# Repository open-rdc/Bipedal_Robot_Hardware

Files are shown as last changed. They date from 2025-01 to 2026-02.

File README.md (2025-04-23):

# Bipedal_Robot_Hardware

RDC_LAB ２足歩行ロボット開発リポジトリ（ハードウェア）

## Circuit
- RDC_Bipedal_Logic
  - Logic回路基板。コンピュータや通信周り
  - Kicad Version: 7
- RDC_Bipedal_Power_Relay_Switch
  - Power回路のリレーのスイッチと、非常停止ボタンの回路
  - Kicad Version: 7
- RDC_Bipedal_Power
  - Power回路図。基板はなく回路図のみ
  - Kicad Version: 9
- RDC_CAN_Chain
  - CANのデイジーチェーン用基板
  - Kicad Version: 9

## LICECNSE

### Hardware
- designer: [Sato Tomoki](https://github.com/tomoki057)

### Circuit
- V1
  - designer: [YusukeYamasaki](https://github.com/Yusuke-Yamasaki-555)
- V2
  - RDC_Bipedal_Logic
    - designer:
      - [Yuya Mochizuki](https://github.com/Mochizuki12)
      - [YusukeYamasaki](https://github.com/Yusuke-Yamasaki-555)
  - RDC_Bipedal_Power_Relay_Switch
    - designer: [YusukeYamasaki](https://github.com/Yusuke-Yamasaki-555)
  - RDC_Bipedal_Power
    - designer: [YusukeYamasaki](https://github.com/Yusuke-Yamasaki-555)
  - RDC_CAN_Chain
    - designer: [YusukeYamasaki](https://github.com/Yusuke-Yamasaki-555)

### maintainer
- [open-rdc/Teams/Humanoid_Development_Team](https://github.com/orgs/open-rdc/teams/humanoid_development_team)

### contributor
- [open-rdc/Teams/Humanoid_Development_Team](https://github.com/orgs/open-rdc/teams/humanoid_development_team)
- [Yuya Mochizuki](https://github.com/Mochizuki12)

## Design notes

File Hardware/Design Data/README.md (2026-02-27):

# RDC-TSUKUBOの全体構成

本ロボットは、**両脚部・胴体部・外装部**の3つの要素から構成される二足歩行ロボットである。

※All Fileにロボット全体のinventorデータを保管しています。ファイルが大きかったので、3つに分けてあります。

---

# 脚部（Leg Assembly）

## ♢ HIP

- RP_Hip-Base  
- RP_Hip-Link-Right  
- RP_Hip-Link-Left  

---

## ♢ Thigh

- RP_Thigh-Base-Right  
- RP_Thigh-Base-Left  
- RP_Thigh-Link  
- RP_Thigh-Base-Cover  
- RP_Thigh-Cover  
- RP_Thigh-Cover-Connect  

---

## ♢ Calf

- RP_Calf-Link-Cover-Inside-Right  
- RP_Calf-Link-Cover-Inside-Left  
- RP_Calf-Link-Cover-Outside-Right  
- RP_Calf-Link-Cover-Outside-Left  
- RP_Calf-Link  
- RP_Calf-Foot  

---

# 胴体部（Body Assembly）

※ 今後記載予定

---

# 外装部（Exterior Assembly）

※ 今後記載予定

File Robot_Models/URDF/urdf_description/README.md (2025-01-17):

# Robot URDF

URDF kitchenを用いて生成してみる。<br>

ref:<br>
- https://qiita.com/Ninagawa123/items/c4643ca92e57c3a45efb
- https://github.com/Ninagawa123/URDF_kitchen

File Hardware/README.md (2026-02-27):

# Design Data
脚部，胴体部，外装部，全体アセンブリのCADデータを保管する

---

# 2DCAD Drawings
JLCCNC(JLCPCB)で使用した2DCAD図面を保管する

---

# stp files
3Dプリンタや、JLCCNC(JLCPCB)で使用したstpファイルを保管する

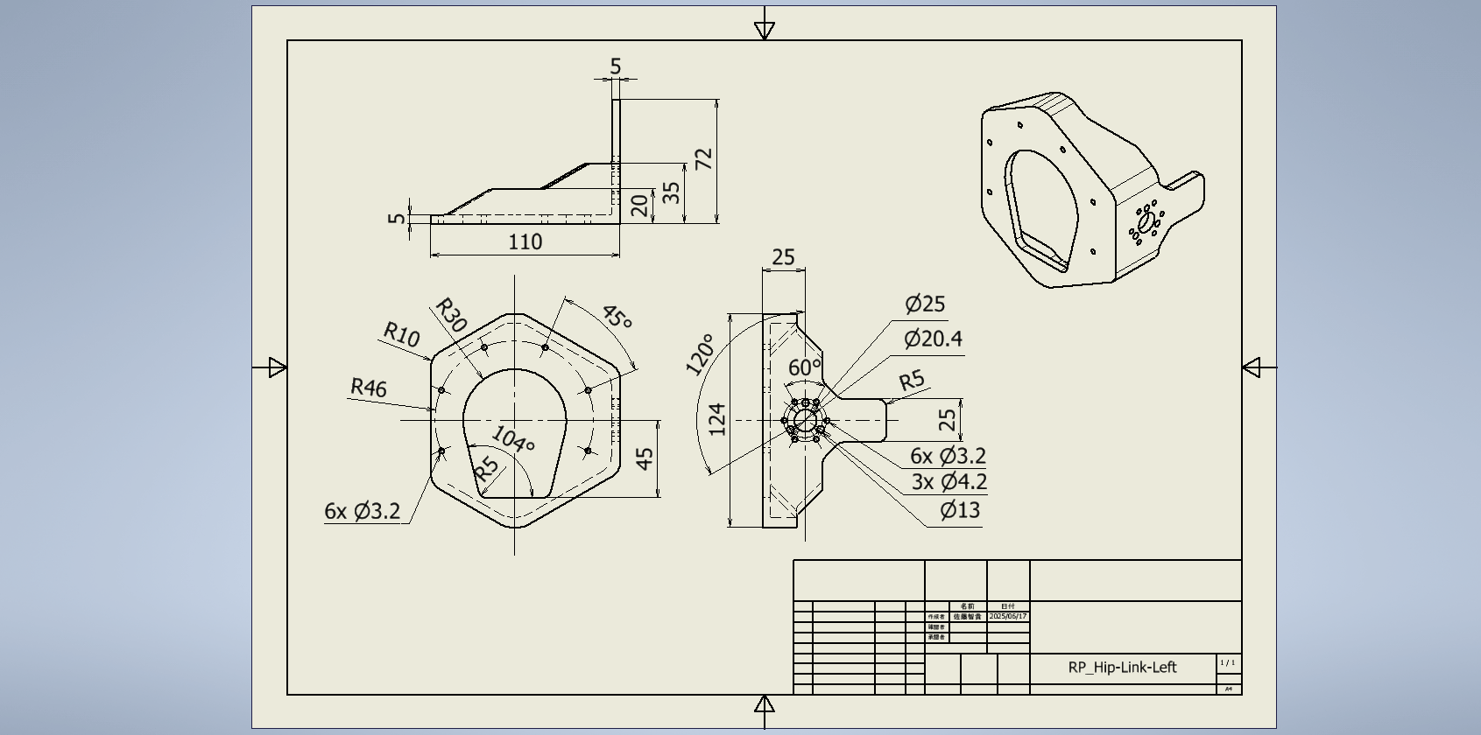
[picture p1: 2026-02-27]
Hardware/2D CAD Drawing/RP_Hip-Link-Left.png

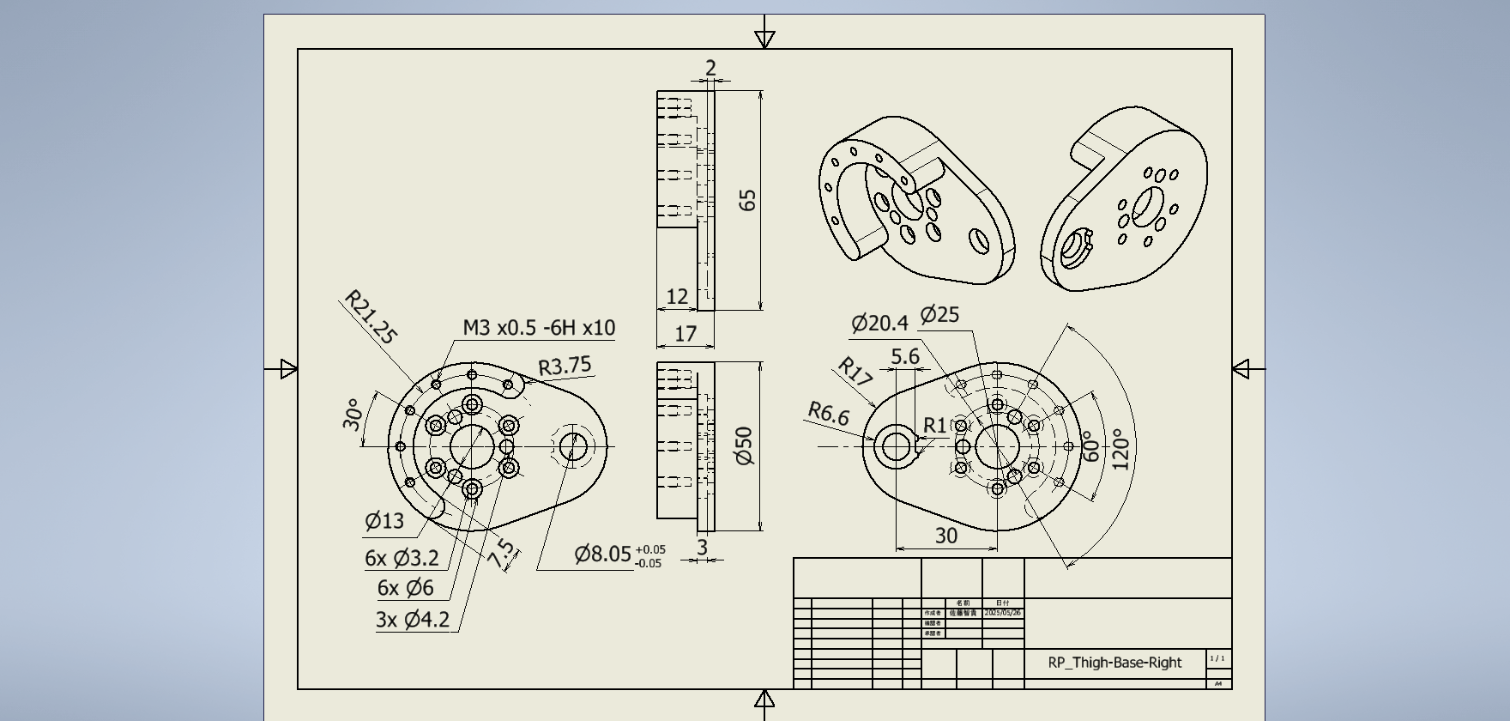
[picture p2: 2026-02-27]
Hardware/2D CAD Drawing/RP_Thigh-Base-Right.png

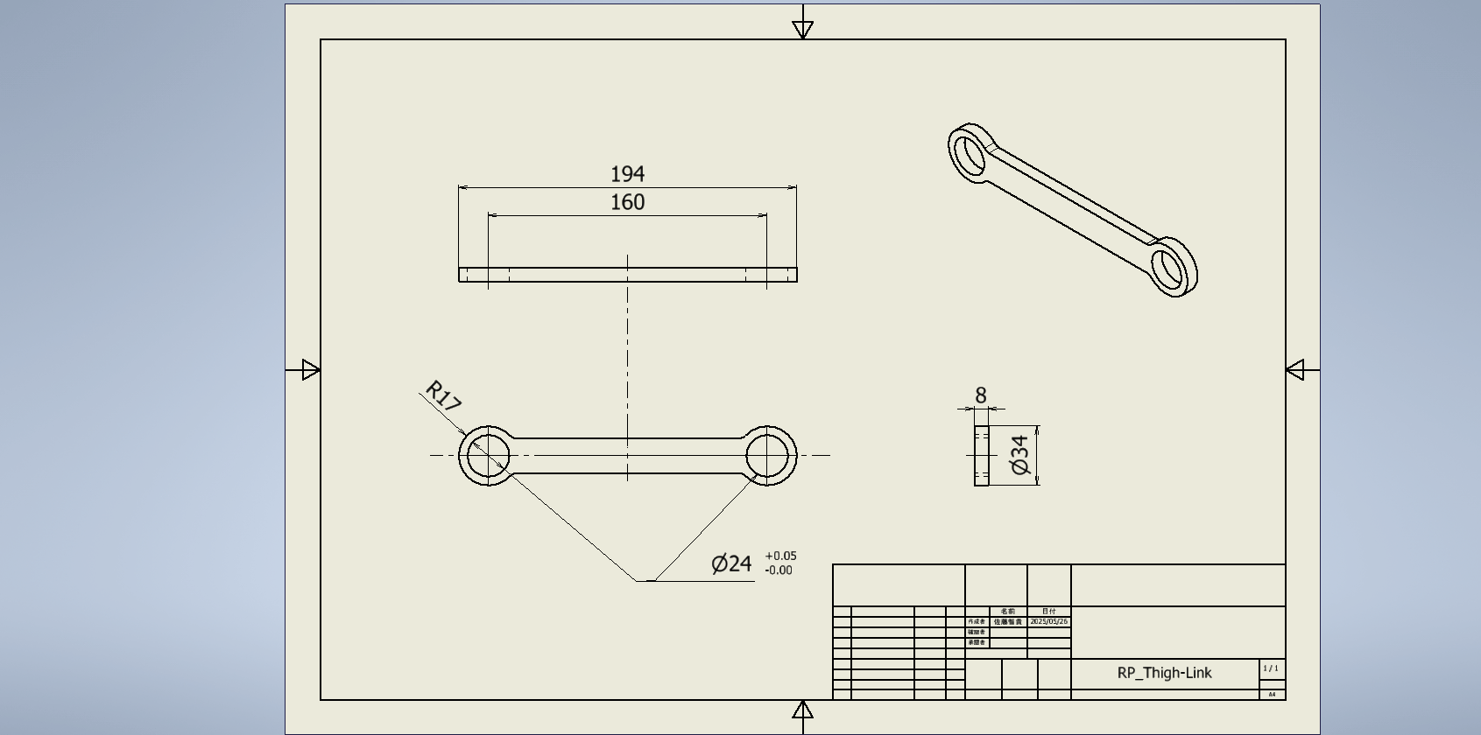
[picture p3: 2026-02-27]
Hardware/2D CAD Drawing/RP_Thigh-Link.png

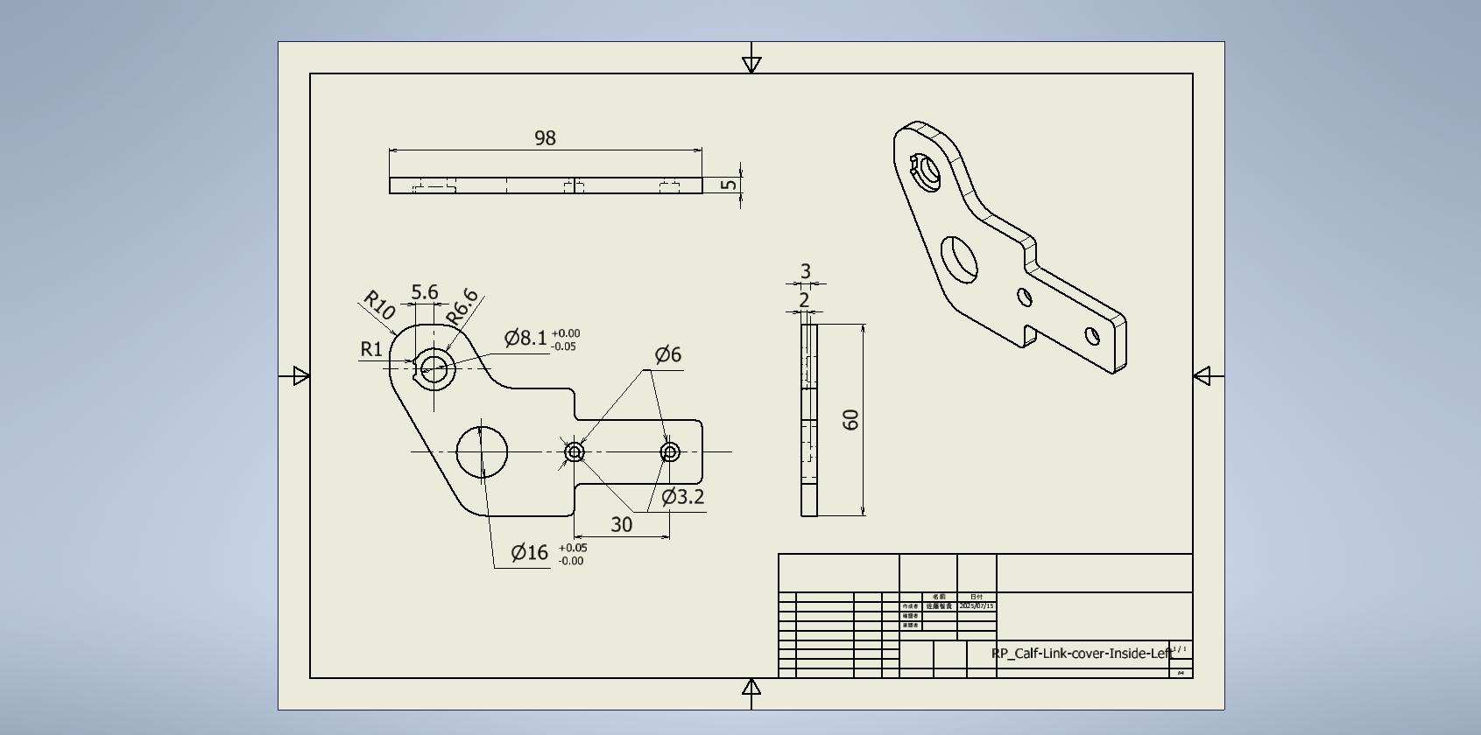
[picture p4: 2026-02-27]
Hardware/2D CAD Drawing/RP_Calf-Link-cover-Inside-Left.png

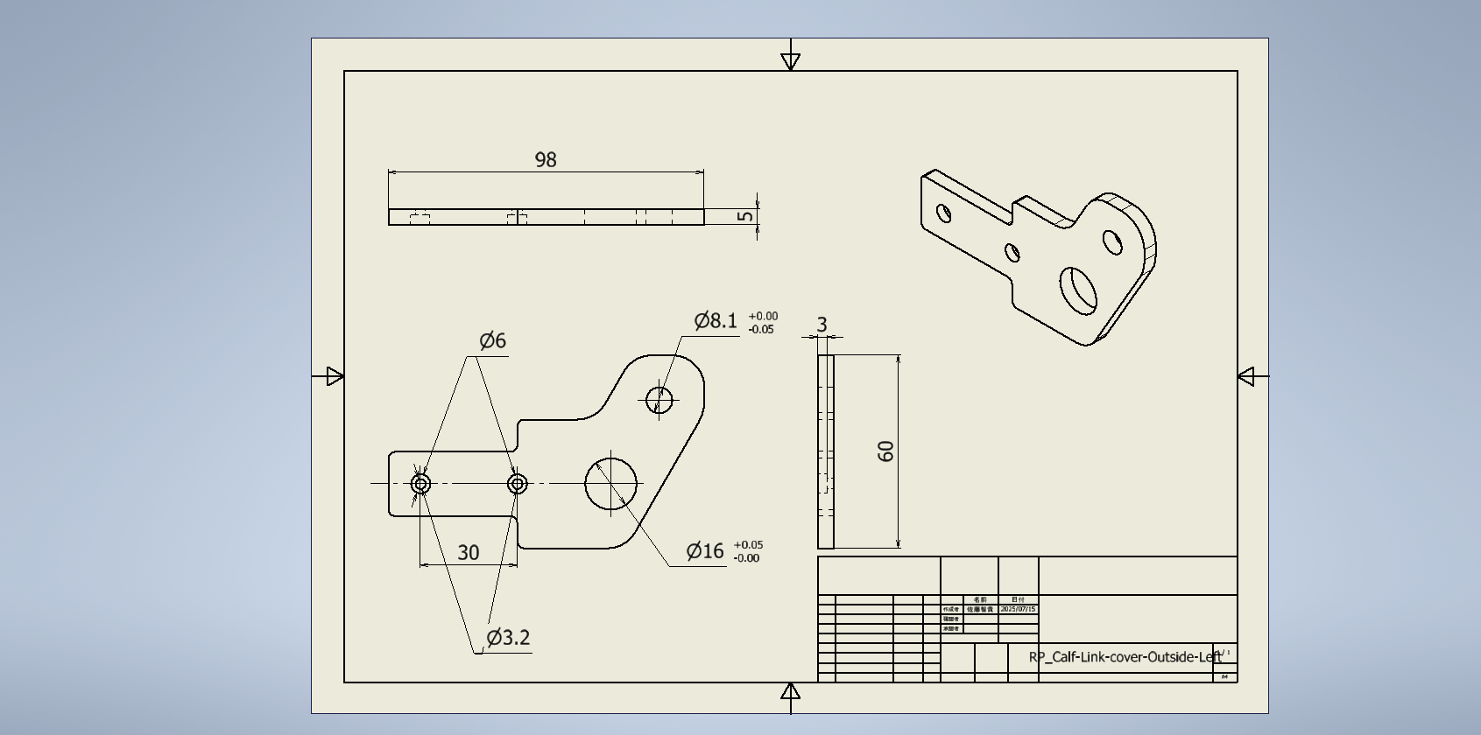
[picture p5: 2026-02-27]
Hardware/2D CAD Drawing/RP_Calf-Link-cover-Outside-Left.png

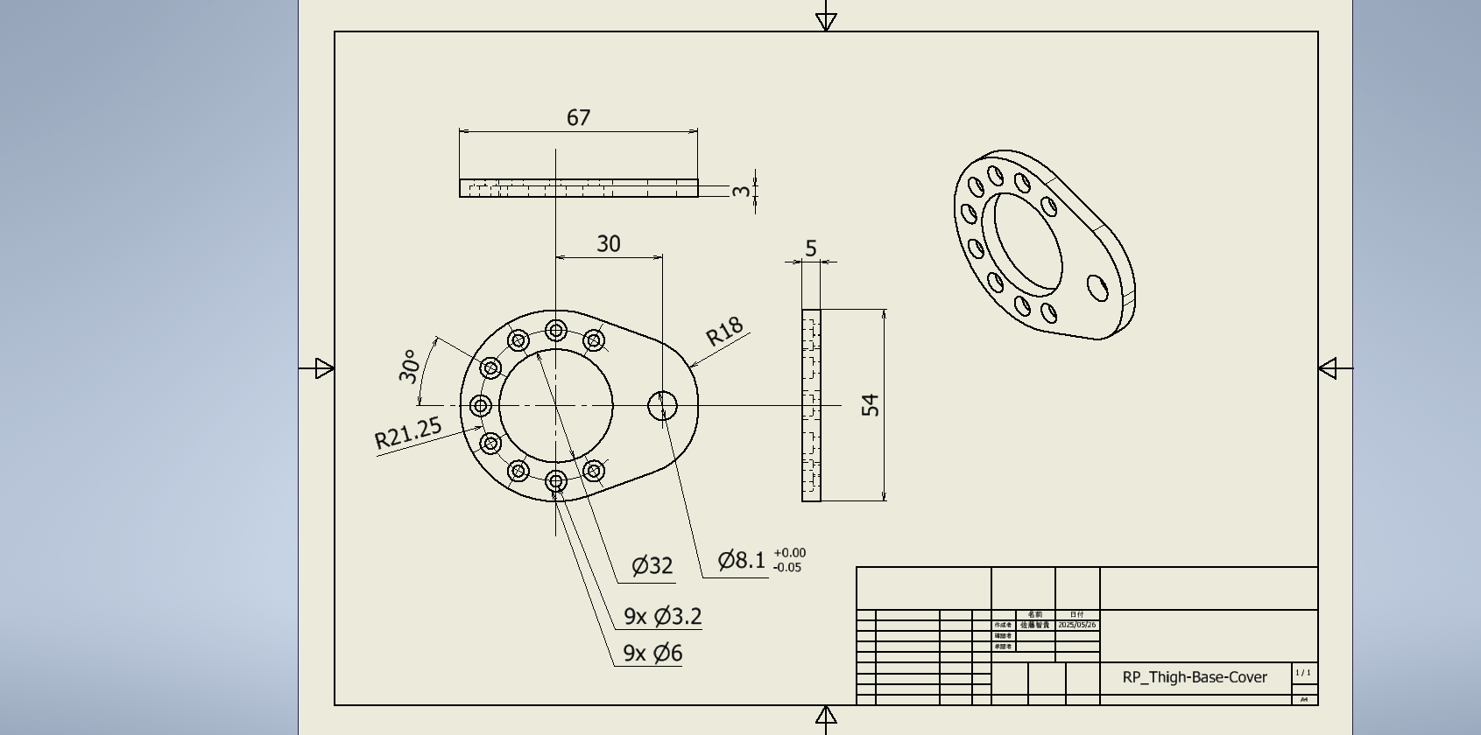
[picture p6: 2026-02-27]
Hardware/2D CAD Drawing/RP_Thigh-Base-Cover.png

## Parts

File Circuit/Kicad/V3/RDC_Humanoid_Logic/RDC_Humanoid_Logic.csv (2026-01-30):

Reference | Qty | Value | DNP | Exclude from BOM | Exclude from Board | Footprint | Datasheet
C1 | 1 | 100uF |  |  |  | Capacitor_THT:CP_Radial_D6.3mm_P2.50mm | https://akizukidenshi.com/catalog/g/g102724/
C2,C6,C7,C15,C16 | 5 | 0.1uF |  |  |  | Capacitor_SMD:C_0603_1608Metric | ~
C3,C9,C11,C12,C18,C20 | 6 | 10uF |  |  |  | Capacitor_SMD:C_0603_1608Metric | ~
C4,C10,C13,C19 | 4 | 1uF |  |  |  | Capacitor_SMD:C_0603_1608Metric | ~
C5,C8,C14,C17 | 4 | 10nF |  |  |  | Capacitor_SMD:C_0603_1608Metric | ~
D1 | 1 | D_Schottky |  |  |  | Diode_SMD:D_SOD-123 | ~
D2,D3,D4 | 3 | LED |  |  |  | LED_SMD:LED_0603_1608Metric | ~
FB1,FB2,FB3,FB4,FB5,FB6,FB7,FB8,FB9,FB10 | 10 | FerriteBead |  |  |  | Inductor_SMD:L_0805_2012Metric | ~
for_PG1 | 1 | M78AR05-0.5 |  |  |  | RDC_humanoid_project:M78A
H1,H2,H3,H4 | 4 | MountingHole |  |  |  | MountingHole:MountingHole_3.2mm_M3 | ~
J1 | 1 | XT60 |  |  |  | Connector_AMASS:AMASS_XT60PW-M_1x02_P7.20mm_Horizontal | ~
J2,J3 | 2 | Conn_01x03 |  |  |  | Connector_JST:JST_XA_S03B-XASK-1_1x03_P2.50mm_Horizontal | https://www.jst-mfg.com/product/pdf/eng/eXA-WB.pdf?67d6871ee54a2
J4 | 1 | Raspi_connect |  |  |  | Connector_PinHeader_2.54mm:PinHeader_2x20_P2.54mm_Vertical | ~
J5 | 1 | 74AHC1G04W5 |  |  |  | Package_TO_SOT_SMD:SOT-23-5 | https://akizukidenshi.com/goodsaffix/74ahc1g04.pdf
J6,J7 | 2 | CH213K |  |  |  | Package_TO_SOT_SMD:SOT-23-3 | https://akizukidenshi.com/goodsaffix/CH213.pdf
Q1,Q2 | 2 | Q_PMOS_GDS |  |  |  | Package_TO_SOT_SMD:TO-252-2 | https://akizukidenshi.com/goodsaffix/TJ60S04M3L_datasheet_ja_20200624.pdf
R1,R2,R7,R8,R12,R13,R14,R15 | 8 | 10k |  |  |  | Resistor_SMD:R_0603_1608Metric | ~
R3,R5,R9 | 3 | 4.7k |  |  |  | Resistor_SMD:R_0603_1608Metric | ~
R4,R6 | 2 | 120 |  |  |  | Resistor_SMD:R_0603_1608Metric | ~
R10,R11 | 2 | 1k |  |  |  | Resistor_SMD:R_0603_1608Metric | ~
SW1,SW2,SW3 | 3 | SW_SPDT |  |  |  | RDC_humanoid_project:Toggle_switch | https://akizukidenshi.com/goodsaffix/2MS1-T1-B4-VS2-Q-E-S.pdf
to_RPI1,to_STM1 | 2 | AE-MYMGK00506ERSR-5V0 |  |  |  | RDC_humanoid_project:AE-MYMGK00506ERSR-5V0
U1,U2 | 2 | ISOW1044 |  |  |  | Package_SO:SOIC-20W_7.5x12.8mm_P1.27mm | https://www.ti.com/lit/ds/symlink/isow1044.pdf?ts=1742141302334
U3 | 1 | NUCLEO-H755ZI-Q_Zio |  |  |  | RDC_humanoid_project:NUCLEO-STM32H755ZI-Q
U4 | 1 | TBD62083AFG |  |  |  | Package_SO:SOP-18_7.495x11.515mm_P1.27mm | https://toshiba.semicon-storage.com/info/datasheet_ja_20160511.pdf?did=29808

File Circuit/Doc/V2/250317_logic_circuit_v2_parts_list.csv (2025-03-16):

 | 私費購入予定 |  |  | 合計金額
↓：要変更 |  |  |  | ¥ 11,558.50 |  |  |  |  | ←：セット商品
 | 購入済み | 系統 | 部品名・部品用途 | 商品名 | 発注会社 | 購入リンク(URL) | 価格(税込み) | 必要数量（最低） | 購入数量 | 購入金額 | 単体重量 [kg] | 総重量 [kg] | 重量（＆関するコメント） | コメント
 | FALSE | コネクタ | 電源用。XT60PW-M | XT60コネクター オス 基板取付用 XT60PW-M | 秋月電子 | https://akizukidenshi.com/catalog/g/g118156/ | ¥ 100.00 | 1 | 1 | ¥ 100.00 |  | 0
 | FALSE | コネクタ | CAN通信用XAヘッダ。S03B-XASK-1 | S03B-XASK-1 | marutsu | https://www.marutsu.co.jp/pc/i/2231712/ | ¥ 67.00 | 2 | 2 | ¥ 134.00 |  | 0 |  | XAコネクタの仕様書：JSTリンク
 | FALSE | コネクタ | CAN通信用XAハウジング。XAP-03V-1 | XAP-03V-1 | marutsu | https://www.marutsu.co.jp/pc/i/953235/ | ¥ 40.00 | 2 | 2 | ¥ 80.00 |  | 0
 | FALSE | コネクタ | CAN通信用XAコンタクト。SXA-001T-P0.6 | SXA-001T-P0.6 | marutsu | https://www.marutsu.co.jp/pc/i/574398/ | ¥ 24.00 | 6 | 6 | ¥ 144.00 |  | 0 |  | コンタクトはまとめ買いのほうがお得なので、それに変えたほうが良い。
 | FALSE | ピンヘッダ | PinHeader_2x20_P2.54mm | ピンヘッダー2x20 (40P) | 秋月電子 | https://akizukidenshi.com/catalog/g/g100080/ | ¥ 50.00 | 1 | 1 | ¥ 50.00 |  | 0
 | TRUE | DCDCコンバータ | 12Vto5V大電流対応降圧モジュール | MYMGK00506ERSR使用 5V出力 最大6A 大電流DCDCコンバーターモジュールキット | 秋月電子 | https://akizukidenshi.com/catalog/g/g115108/ | ¥ 1,320.00 | 2 | 0 | ¥ - |  | 0
 | FALSE | DCDCコンバータ | 12Vto5V PG用DCDCパッケージ | 超高効率DCDCコンバーター(5V0.5A) M78AR05-0.5 | 秋月電子 | https://akizukidenshi.com/catalog/g/g107179/ | ¥ 580.00 | 1 | 1 | ¥ 580.00 | 0.00195 | 0.00195
 | FALSE | スイッチ | 1回路２接点コンピュータ電源用スイッチ | 基板用小型3Pトグルスイッチ 1回路2接点 | 秋月電子 | https://akizukidenshi.com/catalog/g/g100300/ | ¥ 140.00 | 3 | 3 | ¥ 420.00 |  | 0
 | FALSE | コンデンサ | 電源ノイズ対策用コンデンサ | 電源用電解コンデンサー100μF35V105℃ ルビコンZLH | 秋月電子 | https://akizukidenshi.com/catalog/g/g102724/ | ¥ 15.00 | 1 | 1 | ¥ 15.00 |  | 0
 | FALSE | トランジスタ | トランジスタアレイ | 8chソースタイプDMOSトランジスターアレイ TBD62783AFG | 秋月電子 | https://akizukidenshi.com/catalog/g/g111082 | ¥ 70.00 | 1 | 1 | ¥ 70.00 |  | 0
 | FALSE | FET | Back2Backスイッチング用PMOS | PchパワーMOSFET 40V60A TJ60S04M3L | 秋月電子 | https://akizukidenshi.com/catalog/g/g116297/ | ¥ 100.00 | 2 | 2 | ¥ 200.00 |  | 0 |  | 秋月電子で買うから、今のコレ。ゲート・ソース間電圧の定格に近づくほどドレイン・ソース間電圧（＝ロス）が減る。まあ、コレでもほとんど変わらんぐらいなので、良いんでない？
 | FALSE | 抵抗 | チップ抵抗10kΩ（主にPull Up/Down） | RMCF0603FT10K0 | Mouser | https://www.mouser.jp/ProductDetail/SEI-Stackpole/RMCF0603FT10K0 | ¥ 18.70 | 8 | 8 | ¥ 149.60 |  | 0 |  | 複数個買った方がめっちゃ割安。リール（5000個）で買うならコッチ（秋月。仕様が少し違うが問題ない。以下同様）：チップ抵抗 1/10W 10kΩ ￥980
 | FALSE | 抵抗 | チップ抵抗1kΩ（LED） | RMCF0603FT1K00 | Mouser | https://www.mouser.jp/ProductDetail/SEI-Stackpole/RMCF0603FT1K00 | ¥ 18.70 | 2 | 2 | ¥ 37.40 |  | 0 |  | 複数個買った方がめっちゃ割安。リールならコッチ：チップ抵抗 1/10W 1kΩ ￥980
 | FALSE | 抵抗 | チップ抵抗4.7kΩ（LED、Pull Up） | RMCF0603FT4K70 | Mouser | https://www.mouser.jp/ProductDetail/SEI-Stackpole/RMCF0603FT4K70 | ¥ 18.70 | 3 | 3 | ¥ 56.10 |  | 0 |  | 複数個買った方がめっちゃ割安。リールならコッチ：チップ抵抗 1/10W 4.7kΩ ￥980
 | FALSE | 抵抗 | チップ抵抗120Ω（CANの終端抵抗） | RMCF0603FT120R | Mouser | https://www.mouser.jp/ProductDetail/SEI-Stackpole/RMCF0603FT120R?qs=FESYatJ8odLT3vCYyOeKQw%3D%3D | ¥ 18.70 | 2 | 2 | ¥ 37.40 |  | 0 |  | 複数個買った方がめっちゃ割安。
 | FALSE | LED | チップLED（赤＝電源用） | 赤色チップLED [1608] 625nm 120度 OSHR1608（１パック２０個入り） | 秋月電子 | https://akizukidenshi.com/catalog/g/g103978/ | ¥ 200.00 | 1 | 1 | ¥ 200.00 |  | 0 |  | １パック２０個入りの内、実装には３個必要。
 | FALSE | ダイオード | 逆接防止用ショットキーバリアダイオード | チップダイオード 1000V1A GS1010FL（１パック１０個入り） | 秋月電子 | https://akizukidenshi.com/catalog/g/g106014/ | ¥ 100.00 | 1 | 1 | ¥ 100.00 |  | 0 |  | 逆接時に破損してほしいので、安めのやつを選定。１パック１０個の内、実装では１つ使用。
 | FALSE | ダイオード | 逆流防止用ショットキーバリアダイオード | SBRダイオード SBR2U30P1（１パック４個入り） | 秋月電子 | https://akizukidenshi.com/catalog/g/g117096/ | ¥ 100.00 | 1 | 1 | ¥ 100.00 |  | 0 |  | できる限り電圧降下を抑えたいので、順方向電圧が低い良いものを選定。１パック４個の内、使うのは１つ。
 | FALSE | コンデンサ | CAN_Trans用ノイズ対策（高周波） | チップ積層セラミックコンデンサー 0.01μF50V B 1608（１パック５０個入り） | 秋月電子 | https://akizukidenshi.com/catalog/g/g113387/ | ¥ 100.00 | 1 | 1 | ¥ 100.00 |  | 0 |  | １パックの内、実装するのは４個。
 | FALSE | コンデンサ | CAN_Trans用ノイズ対策（高～中周波）、RC回路を形成し電源投入時の電流の立ち上がりを鈍化（突入電流の抑制） | チップ積層セラミックコンデンサー 0.1μF100V X7R 1608（１パック２０個入り） | 秋月電子 | https://akizukidenshi.com/catalog/g/g114559/ | ¥ 150.00 | 1 | 1 | ¥ 150.00 |  | 0 |  | １パックの内、実装するのは５個。
 | FALSE | コンデンサ | CAN_Trans用ノイズ対策（中周波） | チップ積層セラミックコンデンサー 1μF25V X6S 1608（１パック４０個入り） | 秋月電子 | https://akizukidenshi.com/catalog/g/g116993/ | ¥ 120.00 | 1 | 1 | ¥ 120.00 |  | 0 |  | １パックの内、実装するのは４個。
 | FALSE | コンデンサ | CAN_Trans用ノイズ対策（低周波） | チップ積層セラミックコンデンサー 10μF35V X5R 1608（１パック１０個入り） | 秋月電子 | https://akizukidenshi.com/catalog/g/g113161/ | ¥ 150.00 | 1 | 1 | ¥ 150.00 |  | 0 |  | １パックの内、実装するのは６個。
 | FALSE | フェライトビーズ | CAN_Trans用ノイズ対策 | チップインダクター(フェライトビーズ) 330Ω[2012] ムラタBLM21P（１パック２５個入り） | 秋月電子 | https://akizukidenshi.com/catalog/g/g104053/ | ¥ 100.00 | 1 | 1 | ¥ 100.00 |  | 0 |  | １パックの内、実装するのは１０個。
 | TRUE | コンピュータ | 高レベル処理 | Raspberry Pi 5 (8GB) | - | - | ¥ - | 1 | 0 | ¥ - |  | 0
 | FALSE | コンピュータ | 低レベル処理 | NUCLEO-H755ZI-Q | Mouser | https://www.mouser.jp/ProductDetail/STMicroelectronics/NUCLEO-H755ZI-Q?qs=%252B6g0mu59x7KOiBeEHDTYVQ%3D%3D | ¥ 5,264.00 | 1 | 1 | ¥ 5,264.00 |  | 0
 | FALSE | その他 | 基板固定用M3スペーサ | （アキバで調達） |  |  |  |  |  | ¥ - |  | 0
 | FALSE | その他 | 基板固定用M3ナット | （アキバで調達） |  |  |  |  |  | ¥ - |  | 0
 | FALSE | その他 | 基板固定用M3ねじ | （アキバで調達） |  |  |  |  |  | ¥ - |  | 0
 | FALSE | その他 | NUCLEO用ヒートシンク | （アキバで調達） |  |  |  |  |  | ¥ - |  | 0
 | FALSE | IC | 絶縁DCDCコンバータ付き絶縁CANトランシーバ | ISOW1044BDFMR | Mouser | https://www.mouser.jp/ProductDetail/Texas-Instruments/ISOW1044BDFMR?qs=Li%252BoUPsLEnsRP1xV2fQwnw%3D%3D | ¥ 1,600.50 | 2 | 2 | ¥ 3,201.00 |  | 0
 | FALSE |  |  |  |  |  |  |  |  | ¥ - |  | 0
 | FALSE |  |  |  |  |  |  |  |  | ¥ - |  | 0
 | FALSE |  |  |  |  |  |  |  |  | ¥ - |  | 0
 | FALSE |  |  |  |  |  |  |  |  | ¥ - |  | 0
 | FALSE |  |  |  |  |  |  |  |  | ¥ - |  | 0
 | FALSE |  |  |  |  |  |  |  |  | ¥ - |  | 0
 | FALSE |  |  |  |  |  |  |  |  | ¥ - |  | 0
 | FALSE |  |  |  |  |  |  |  |  | ¥ - |  | 0
 | FALSE |  |  |  |  |  |  |  |  | ¥ - |  | 0
 | FALSE |  |  |  |  |  |  |  |  | ¥ - |  | 0
 | FALSE |  |  |  |  |  |  |  |  | ¥ - |  | 0
 |  |  |  |  |  |  |  |  | 最低合計金額： | ¥11,558.50
 |  |  |  |  |  |  |  | 購入先別金額 | 秋月電子： | ¥ 2,455.00 |  | 送料リスト： | Mouser： | ¥2,000.00
 |  |  |  |  |  |  |  |  | Mouser： | ¥ 8,745.50 |  | （税込み） | 秋月電子： | 500 or 600 x 個口数
 |  |  |  |  |  |  |  |  | marutsu： | ¥ 358.00 |  |  | marutsu： | 550 (宅急便) or 385 (ネコポス)
 |  |  |  |  |  |  |  |  |  |  |  | 送料無料ライン： | Mouser： | ¥6,600.00
 |  |  |  |  |  |  |  |  | SUM | ¥ 11,558.50 |  | （税込み） | 秋月電子： | ¥11,000.00
 |  |  |  |  |  |  |  |  |  |  |  |  | marutsu： | ¥3,300.00

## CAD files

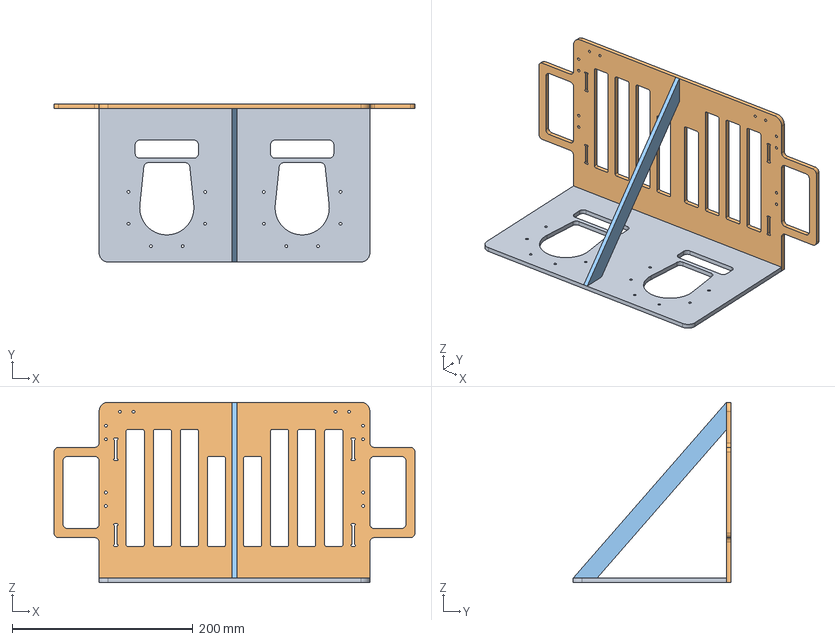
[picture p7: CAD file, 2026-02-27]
Hardware/stp files/Assembly_Waist.stp
400.0 x 175.0 x 200.0 mm
RP_Waist-Under
RP_Waist-Avobe
RP_Waist-Diagonal-material

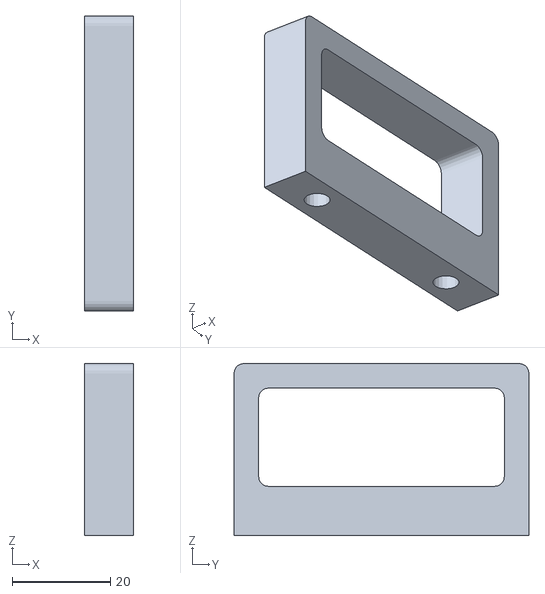
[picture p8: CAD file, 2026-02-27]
Hardware/Design Data/Body Assembly/BP_BOX-handle.stl
10.0 x 60.0 x 35.0

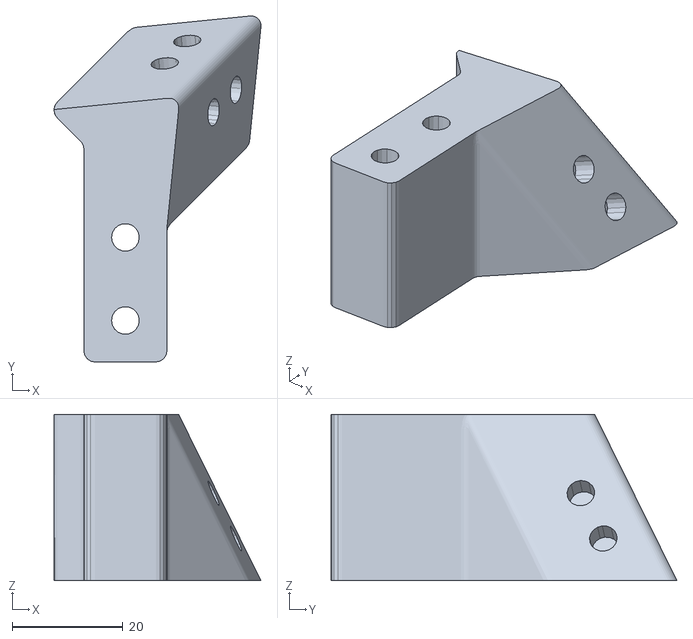
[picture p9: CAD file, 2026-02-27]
Hardware/Design Data/Exterior Assembly/EX-L-Connect-Back-Right.stl
37.4 x 62.5 x 30.0

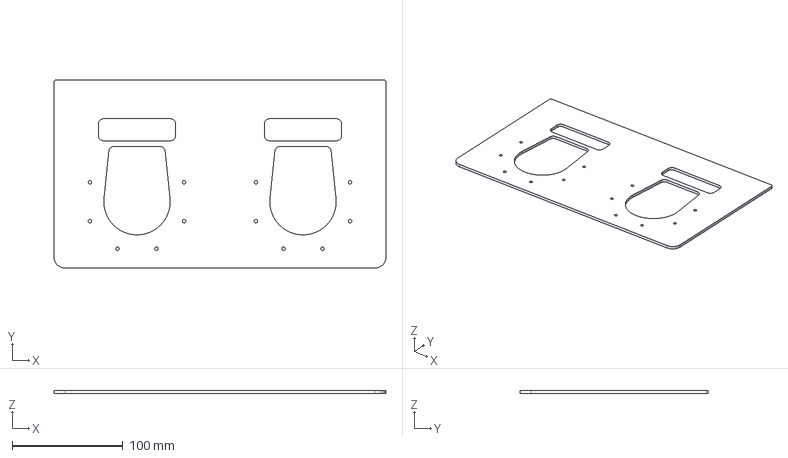
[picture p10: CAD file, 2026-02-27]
Hardware/Design Data/Leg Assembly/RP_Waist-Under-ver2.stp
300.0 x 170.0 x 3.00 mm

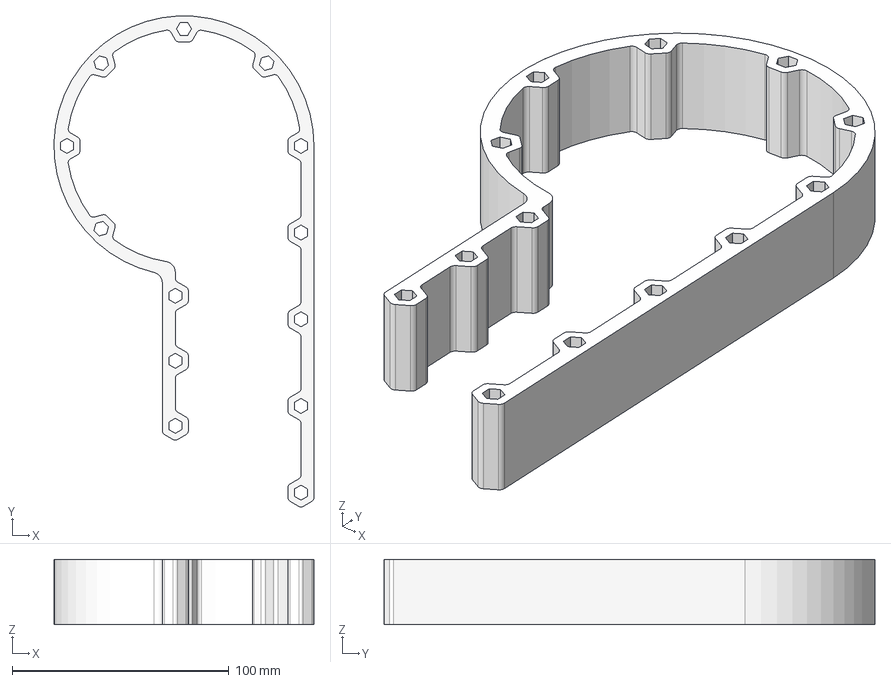
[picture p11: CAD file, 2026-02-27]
Hardware/stp files/RP_Thigh-cover-connect.stp
120.0 x 226.5 x 30.0 mm

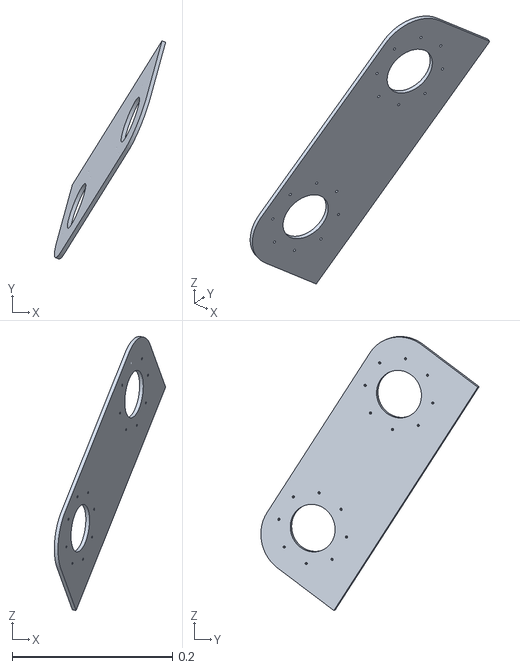
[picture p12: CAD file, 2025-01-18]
Robot_Models/URDF/urdf_description/meshes/body/b_right-wr2left-wr__legparts_09(six).stl
0.139 x 0.273 x 0.342

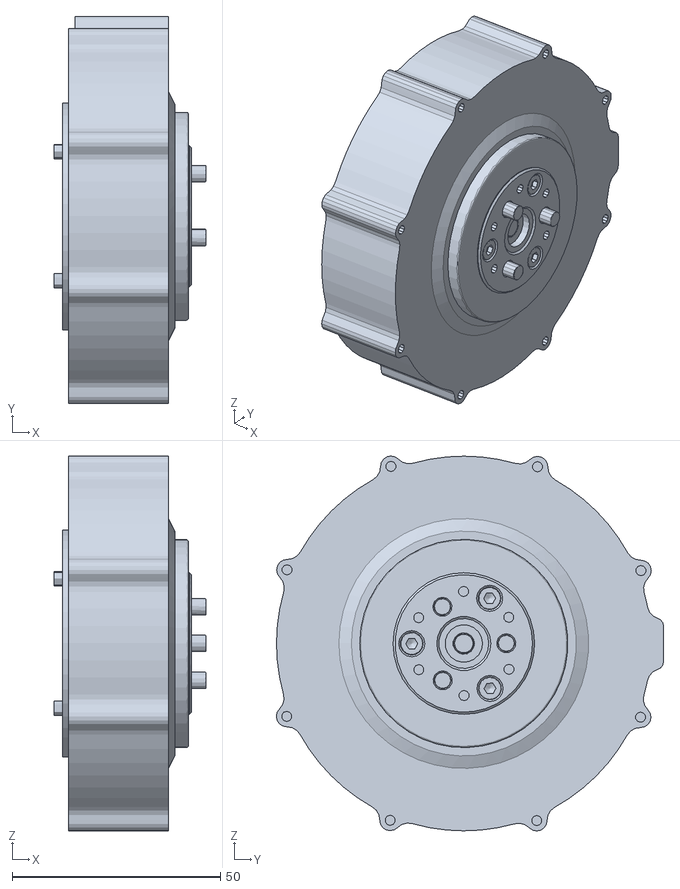
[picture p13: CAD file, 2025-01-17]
Robot_Models/URDF/urdf_description/meshes/r-leg/mm/mr_j_wr__8108-8.stl
36.5 x 93.0 x 90.1

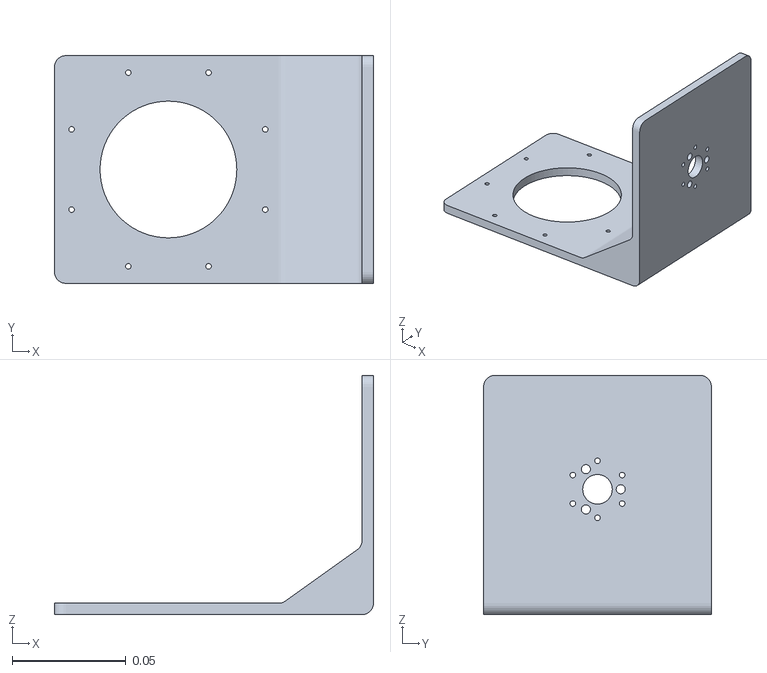
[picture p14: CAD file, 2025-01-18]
Robot_Models/URDF/urdf_description/meshes/r-leg/r_l_wp2wr__legparts_07(four).stl
0.14 x 0.1 x 0.105

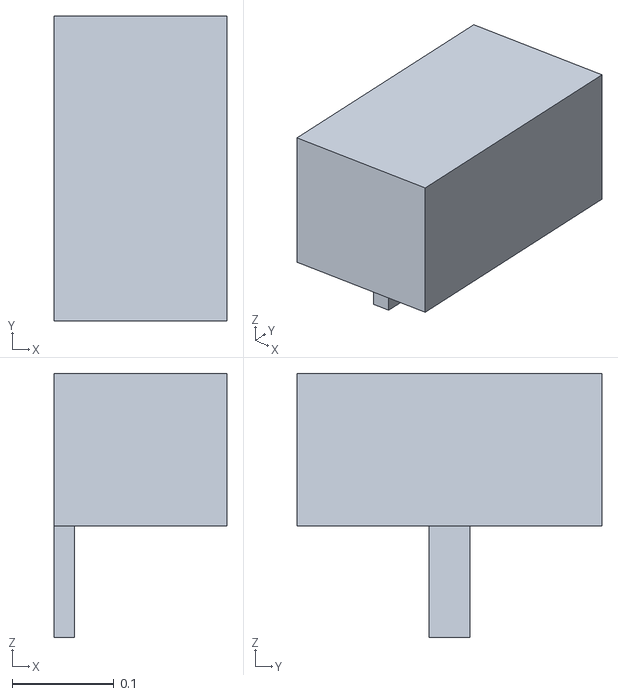
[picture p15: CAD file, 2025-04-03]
Robot_Models/URDF/urdf_simple-model/meshes/stl/body_luggage.stl
0.17 x 0.3 x 0.26

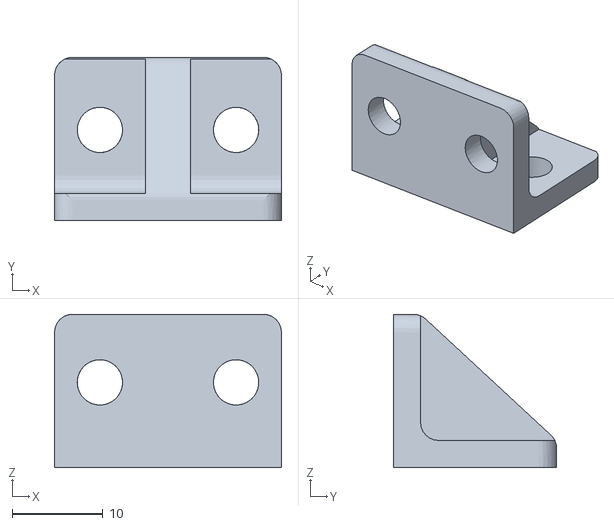
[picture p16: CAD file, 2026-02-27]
Hardware/Design Data/Body Assembly/BP_L.stl
25.0 x 18.0 x 16.9

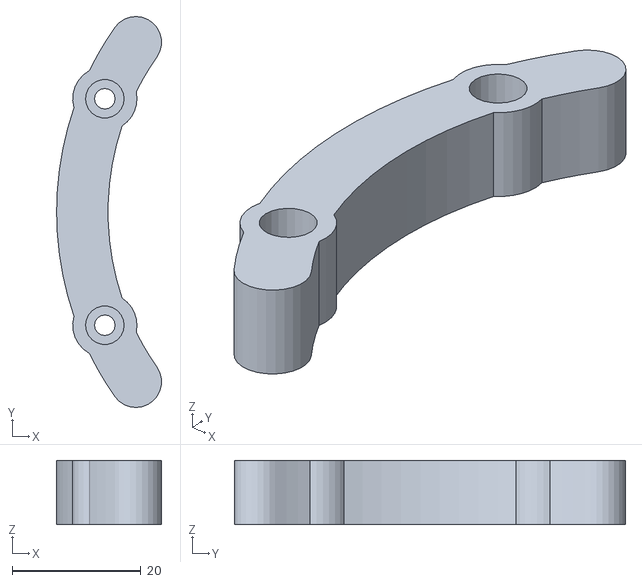
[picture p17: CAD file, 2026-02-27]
Hardware/Design Data/Leg Assembly/RP_Hip-Link-Limit-short.stl
16.3 x 60.8 x 10.0

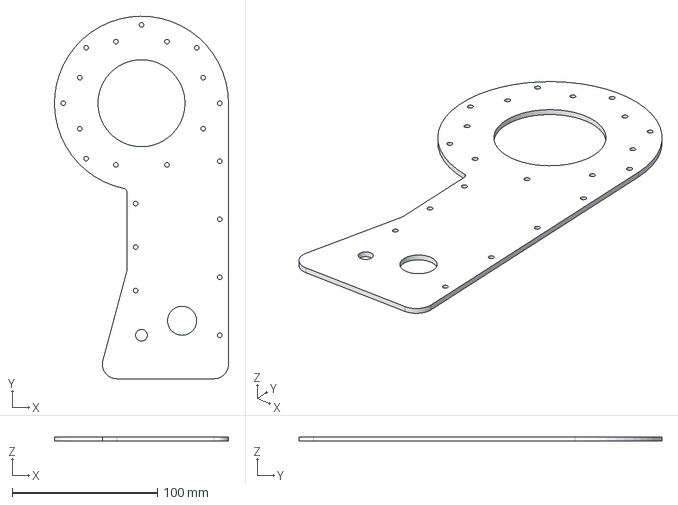
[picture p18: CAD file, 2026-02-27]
Hardware/stp files/RP_Thigh-cover.stp
120.0 x 250.0 x 3.00 mm

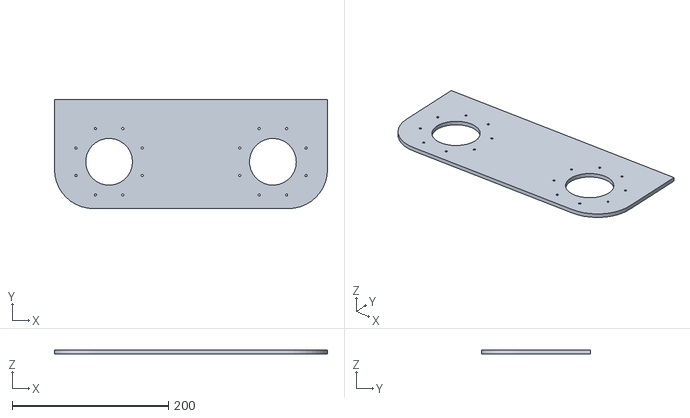
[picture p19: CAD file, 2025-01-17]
Robot_Models/URDF/urdf_description/meshes/body/mb_right-wr2left-wr__legparts_09(six).stl
350.0 x 140.0 x 5.00

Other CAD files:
Hardware/2D CAD Drawing/Assembly_All.dwg
Hardware/2D CAD Drawing/Assembly_Leg-Right.dwg
Hardware/2D CAD Drawing/RP_Hip-Link-Left.dwg
Hardware/2D CAD Drawing/RP_Hip-Base.dwg
Hardware/Design Data/Exterior Assembly/EX-L-Connect-Back-Left.stl
Hardware/2D CAD Drawing/AA30306.dwg
Hardware/2D CAD Drawing/RP_Calf-Link-cover-Inside-Left.dwg
Hardware/2D CAD Drawing/RP_Calf-Link-cover-Inside-Right.dwg
Hardware/2D CAD Drawing/RP_Calf-Link-cover-Outside-Left.dwg
Hardware/2D CAD Drawing/RP_Calf-Link-cover-Outside-Right.dwg
Hardware/2D CAD Drawing/RP_Hip-Link-Right.dwg
Hardware/2D CAD Drawing/RP_Thigh-Base-Cover.dwg
Hardware/2D CAD Drawing/RP_Thigh-Base-Right.dwg
Hardware/2D CAD Drawing/RP_Thigh-Base_Left.dwg
Hardware/2D CAD Drawing/RP_Thigh-Link.dwg
Hardware/2D CAD Drawing/RP_Thigh-cover.dwg
Hardware/2D CAD Drawing/RP_Waist-Avobe-ver2-1.dwg
Hardware/2D CAD Drawing/RP_Waist-Under-ver2.dwg
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

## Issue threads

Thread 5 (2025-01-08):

SteadyWin GIM8108-8を動かしてみる

HarukiOgawa1, 2025-01-08:
## 動作環境
Steadywin-GIM8108-8
安定化電源 (SPS-3010 0-30V 0-10A)
USBケーブル (type A to C)
XT30PB(2+2)-M

## やること

- [x] とりあえず、電源とUSB通信して動かす

- [x] そのあと、CAN通信で動かす

- [x] 動作環境を整える

　安定化電源　（KX-100L）
　USBケーブル
　電源ケーブル　https://www.amazon.co.jp/dp/B08FSYZBTD?ref=ppx_yo2ov_dt_b_fed_asin_title
　XT30PB(2+2)-M　受けに合うように
　XT30(2+2)-F メス
　CANケーブル　https://www.amazon.co.jp/dp/B0BQ5G3KLR?ref=ppx_yo2ov_dt_b_fed_asin_title

## 参考
[Steadywin-GIM8108-8を回す odrivetool編](https://zenn.dev/robohase01/articles/6eae2db2af93d8)
[Steadywin-GIM8108-8を回す ROS 2編](https://zenn.dev/robohase01/articles/4697e25ca87c76)

HarukiOgawa1, 2025-01-08:
wslの場合
- wslで行う場合
https://learn.microsoft.com/ja-jp/windows/wsl/connect-usb
USBに接続して許可する　Sharedはまだ使えない状態
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

```
PS C:\Users\azara> usbipd list
Connected:
BUSID  VID:PID    DEVICE                                                        STATE
1-2    1209:0d32  USB シリアル デバイス (COM4), CyberBeast Motor Driver Device          Shared
1-3    04f2:b725  Integrated Camera, Camera DFU Device                          Not shared
2-1    0000:3825  USB 入力デバイス                                                    Not shared
2-3    27c6:550a  Goodix fingerprint                                            Not shared
2-4    0bda:4853  Realtek Bluetooth Adapter                                     Shared

Persisted:
GUID                                  DEVICE
6e8e7fe5-4833-43df-853f-f201de69bc54  USB Serial Converter A, USB Serial Converter B, USB Seria...

PS C:\Users\azara> usbipd attach --wsl --busid 1-2
usbipd: info: Using WSL distribution 'Ubuntu-22.04' to attach; the device will be available in all WSL 2 distributions.
usbipd: info: Using IP address 172.26.64.1 to reach the host.
PS C:\Users\azara> usbipd list
Connected:
BUSID  VID:PID    DEVICE                                                        STATE
1-2    1209:0d32  USB シリアル デバイス (COM4), CyberBeast Motor Driver Device          Attached
1-3    04f2:b725  Integrated Camera, Camera DFU Device                          Not shared
2-1    0000:3825  USB 入力デバイス                                                    Not shared
2-3    27c6:550a  Goodix fingerprint
    Not shared
2-4    0bda:4853  Realtek Bluetooth Adapter
    Shared

Persisted:
GUID                                  DEVICE
6e8e7fe5-4833-43df-853f-f201de69bc54  USB Serial Converter A, USB Serial Converter B, USB Seria...

```

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

Yusuke-Yamasaki-555, 2025-01-26:
メモ:
odrive can bus guide: https://docs.odriverobotics.com/v/latest/guides/can-guide.html

HarukiOgawa1, 2025-01-31:
Windows11 PCのwsl2上でCAN通信を行う場合，以下の方法でwslのカーネルをビルドしないといけないのがわかった．
https://github.com/open-rdc/Bipedal_Robot_Hardware/issues/5#issuecomment-2576463189 までは大丈夫だが，wsl側でCAN-USBが認識されない．
https://blog.hcmos.jp/posts/can_with_wsl/

Yusuke-Yamasaki-555, 2025-02-03:
https://github.com/siddarthiyer/ODrive-STM32-CAN-Driver

HarukiOgawa1, 2025-02-07:
メモ　CANのコマンド
- CANデバイスの確認　can0が表示されれば，デバイスが認識されている
```ls /sys/class/net```
- 物理CANデバイスのセットアップ（can0の場合）

1. CANインターフェイスを立ち上げ　500000は500kbpsの通信速度
```sudo ip link set can0 up type can bitrate 500000```
か
```
sudo ip link set can0 type can bitrate 500000
sudo ip link set can0 up
```
2. CANインターフェイスをダウン
```sudo ip link set can0 down```
3. CAN受信確認
```candump can0```

- CANドライバのロード（必要であれば）
```
sudo modprobe can
sudo modprobe can_raw
sudo modprobe can_dev

# USB-CANデバイスの場合，slcan（シリアルCAN），peak_usb（PEAK社製デバイス用）など，デバイスに応じたドライバも必要らしい
sudo modprobe slcan
```

HarukiOgawa1, 2025-04-08:
https://github.com/open-rdc/Bipedal_Robot_Hardware/issues/5#issuecomment-2642500563
以前， [DSD TECH SH-C30A USB-CAN バス アダプター](https://www.amazon.co.jp/dp/B0BQ5G3KLR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)で通信できないとコメントしたが，https://github.com/open-rdc/Bipedal_Robot_Software/issues/2 のようにこの時に試していたプログラムが間違っていた可能性が高い．

Closed 2025-04-08.

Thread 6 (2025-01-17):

二足歩行シミュレーション

tomoki057, 2025-01-17:
Assembly5の歩行シミュレーションを行い, 現状の設計段階で歩行可能かどうかの確認をしたい.

レポジトリにCadファイルを追加しました.

Yusuke-Yamasaki-555, 2025-01-17:
stlファイルの出力、完了。
これらをmeshとしてurdfを作成予定。

（まだ未push。pushの権限がない？）

Yusuke-Yamasaki-555, 2025-01-19:
出力したstlが、基準座標があらぬところだったり座標系がロボットに適していなかったりしたので、簡易モデルを自分で作った。

寸法は Assembly5 におおよそ合わせた。関節の回転角度制限はURDF内で数値的に行うことにする。

簡易モデルはHardwareというよりソフトの検証用にあるので、モデルの情報はソフトウェア用の別リポジトリにある。
https://github.com/open-rdc/Bipedal_Robot_Software/tree/main/robot_description/simple_model

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

Yusuke-Yamasaki-555, 2025-01-19:
本リポジトリにある簡易モデルは古いものとなるので、削除する予定。

HarukiOgawa1, 2025-01-21:
作成してもらったモデルで歩行できるか検証中
https://github.com/open-rdc/Bipedal_Robot_Software/tree/walk_with_genesis

https://github.com/user-attachments/assets/a0a3f8eb-0e31-41fb-940b-d6aed0269c3e

yasuohayashibara, 2025-01-21:
興味深いですね．

それなりにバランスを取ろうとしていますね．

HarukiOgawa1, 2025-01-22:
以下の既存環境への外部からのモデルのインポートする方法で学習してみた．
https://github.com/open-rdc/IsaacLabInvestigation/issues/4

↓学習環境
https://github.com/open-rdc/IsaacLab/tree/rdclab_bipedal_robot

結果は↓の動画のように膝立ちで歩くようになった．考察だが，feet_air_time（足を上げる時間）の報酬関数で現在のモデルの地面に当たるのがhttps://github.com/open-rdc/Bipedal_Robot_Software/blob/main/robot_description/simple_model/meshes/stl/link_kp2heel.stl になっているため，足先の先端のモデルを分けた方が良いと思う．

https://github.com/user-attachments/assets/164a9f6d-4326-4bb5-905a-603920f69059

Yusuke-Yamasaki-555, 2025-01-22:
@HarukiOgawa1 ちなみに、各関節トルクってどうしてます？

HarukiOgawa1, 2025-01-22:
各関節トルクは以下の定常トルクの7.5 [Nm]にしました．
参考にしたREADME
https://github.com/open-rdc/Bipedal_Robot_Software/tree/main/robot_description/simple_model

https://github.com/open-rdc/IsaacLab/blob/rdclab_bipedal_robot/source/extensions/omni.isaac.lab_assets/omni/isaac/lab_assets/unitree.py
```
RDCLab_bipedal_robot_CFG = ArticulationCfg(
    spawn=sim_utils.UsdFileCfg(
        usd_path=f"/workspace/isaaclab/source/extensions/omni.isaac.lab_assets/data/Robots/RDCLab/rdclab_bipedal_robot.usd",
        activate_contact_sensors=True,
        rigid_props=sim_utils.RigidBodyPropertiesCfg(
            disable_gravity=False,
            retain_accelerations=False,
            linear_damping=0.0,
            angular_damping=0.0,
            max_linear_velocity=1000.0,
            max_angular_velocity=1000.0,
            max_depenetration_velocity=1.0,
        ),
        articulation_props=sim_utils.ArticulationRootPropertiesCfg(
            enabled_self_collisions=False, solver_position_iteration_count=8, solver_velocity_iteration_count=4
        ),
    ),
    init_state=ArticulationCfg.InitialStateCfg(
        pos=(0.0, 0.0, -0.07),
        joint_pos={
            ".*r_waist_roll"    :0.0,
            ".*r_waist_pitch"   :-0.7,
            ".*r_knee_pitch"    :1.5,
            ".*l_waist_roll"    :0.0,
            ".*l_waist_pitch"   :-0.7,
            ".*l_knee_pitch"    :1.5,
        },
        joint_vel={".*": 0.0},
    ),
    soft_joint_pos_limit_factor=0.9,
    actuators={
        "legs": ImplicitActuatorCfg(
            joint_names_expr=[
                ".*r_waist_roll",
                ".*r_waist_pitch",
                ".*r_knee_pitch",
                ".*l_waist_roll",
                ".*l_waist_pitch",
                ".*l_knee_pitch",
            ],
            effort_limit=7.5,
            velocity_limit=10.0,
            stiffness=120.0,
            damping=5.0,
            armature=0.01,
        ),
    },
)
```

Yusuke-Yamasaki-555, 2025-01-22:
了解です。URDFでもトルクと角速度を設定してありますが、labの設定のほうが優先される感じですか？

HarukiOgawa1, 2025-01-22:
はい，現段階だとlabの設定が優先されていると思います．

HarukiOgawa1, 2025-01-22:
以下と同じ状況でトルクを7.5 -> 20 [Nm]，角速度を10 -> 20 [rad/s]に変更してみた学習結果
https://github.com/open-rdc/Bipedal_Robot_Hardware/issues/6#issuecomment-2607393364

https://github.com/user-attachments/assets/490d8da0-080f-4621-ac4e-ee8d8ef3180c

Yusuke-Yamasaki-555, 2025-01-22:
脛と足首を別パーツ化しました。

Yusuke-Yamasaki-555, 2025-01-22:
> 以下と同じ状況でトルクを7.5 -> 20 [Nm]，角速度を10 -> 20 [rad/s]に変更してみた学習結果 [#6 (comment)](https://github.com/open-rdc/Bipedal_Robot_Hardware/issues/6#issuecomment-2607393364)
>
>  250122_bipedal_not_walk_isaaclab_e20v20.mp4

修正前のurdfなので断定はできませんが、遊脚の時間が少し長いように思います。歩行周期をもう少し短くして遊脚時間を減らせれば、より負担がかからないような気がしますね

HarukiOgawa1, 2025-01-22:
https://github.com/open-rdc/IsaacLabInvestigation/issues/4 のURDFをUSDに変換する際に以下のようなエラーが発生した．

[Error] [omni.importer.urdf] *** URDF has multiple links that are not connected to a joint

原因は，URDFファイル内でジョイントを介さずに接続されていないリンクがあるみたいです．
_heel2endあたりかと

Yusuke-Yamasaki-555, 2025-01-22:
おそらく修正完了。
link名が不足していました。

HarukiOgawa1, 2025-01-23:
heel2end以外に転倒判定を追加，各リンクの質量を半分，トルク20[Nm]，角速度20[rad/s]で学習した結果
今後の検証：各関節の可動域の制限，足上げの時間の調整

https://github.com/user-attachments/assets/6d681d43-f36f-45bb-a8d8-125bfe558a94

Yusuke-Yamasaki-555, 2025-01-23:
リンクの質量は未変更ですか？

HarukiOgawa1, 2025-01-23:
とりあえず，mass valueの値を半分にしました．

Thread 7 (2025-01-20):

回路周りの発注

Yusuke-Yamasaki-555, 2025-01-20:
発注リスト
https://docs.google.com/spreadsheets/d/1lJcXPqMS-PpS88h2CHwjywfNJw795AIvWntSnHbxz7g/edit?gid=0#gid=0

発注する回路部品を決めて、発注する

Yusuke-Yamasaki-555, 2025-01-23:
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

回路構成図メモ

Yusuke-Yamasaki-555, 2025-01-23:
回路構成図の清書
部品の選定はもうちょい待って

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

yasuohayashibara, 2025-01-23:
12Vは5Vで良いのでは？
5VだとUSBのバッテリが使用できますし，ON/OFFが必要であればスイッチ付きのケーブルもあります．

参考まで
https://amzn.asia/d/5UwHIir

Yusuke-Yamasaki-555, 2025-01-23:
ありがとうございます。
おっしゃる通り、バッテリを各コンピュータにつなげたほうが楽ですし良いかもしれません...

12Vを選択した理由としましては、ラズパイ5の電源が5V, 5Aを要求している点にあります。
この要求を満たすために、容量が大きなバッテリーから降圧させてGPIOから給電する方法を考えていました。
ただ、5Aも消費しないのであれば不要ですし、ラズパイ4にすれば（性能は落ちますが）解決する問題でもあるので...

もう少し検討してみます

Yusuke-Yamasaki-555, 2025-01-23:
リレーに関して：
- リレーを使う際はサージキラー（コイルサージ吸収回路）を用いることが効果的であり、リレーによってはそれが指示されている。
- 無視しても使えるかもしれない。

Yusuke-Yamasaki-555, 2025-01-23:
部品選定の中で実現が難しい箇所が幾つか見つかったので、ブラッシュアップを行う。

Yusuke-Yamasaki-555, 2025-01-23:
version 1.1
- 48V 100A に耐えられるような非常停止やトグルスイッチがなかったので、パワーリレーでスイッチングする、MEVIUSと同じような構成に変更
- sub-computer - main-PC 間の通信の配線を忘れていたので追記

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

部品選定は、おおよそ目星がついた。
複数の案があるパーツに関しては、サクッと一旦決めてしまおうと思う。
ただ、初めての回路設計と不慣れであるため、多くの見落としや不足点・問題点があるものと思います。
回路設計に関して、アドバイスをいただけますと幸いです。
https://docs.google.com/spreadsheets/d/1lJcXPqMS-PpS88h2CHwjywfNJw795AIvWntSnHbxz7g/edit?usp=sharing

PS:
ラズパイの電源を5Vにするご提案に関してなのですが、パワーリレーでスイッチングを行う都合上、5Vより12Vのほうが部品選定の関係から使わざる負えないと判断しました。
FETスイッチモジュールを使うという案も一応あるのですが、この高電圧高電流に耐えられるものは簡単に見つかりそうもないです。

Yusuke-Yamasaki-555, 2025-01-24:
発注完了

version1.1の回路を決定

https://docs.google.com/spreadsheets/d/1lJcXPqMS-PpS88h2CHwjywfNJw795AIvWntSnHbxz7g/edit

Closed 2025-01-24.

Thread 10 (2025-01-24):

回路v1.1の検証

Yusuke-Yamasaki-555, 2025-01-24:
回路v1.1が決まった。
この回路の問題点や改善点を洗い出し、v1.2~ につなげる。そのためのissue。

挙がった問題や改善点は、以下の詳細設計のissueに入っていくだろう。
issue: [回路v1.1の詳細設計](https://github.com/open-rdc/Bipedal_Robot_Hardware/issues/9)

Yusuke-Yamasaki-555, 2025-01-25:
Logicの電源に関して
- コンピュータの電源は、5Vであるならモバイルバッテリーが良いのではないか、という指摘
  - 12Vから降圧するよりも簡単で取り回しが良いから？
  - 他への供給をおこなうことで発生するであろうノイズが乗らないから？
    - コレに関しては、ノイズ源の有無で変わると思う。現状、モータは別電源。ただしリレーのコイル側を含んでいる。

Yusuke-Yamasaki-555, 2025-01-28:
あと、V1.1の、コイル側につけるべきサージキラーが接点側についている。
修正するべき。

Yusuke-Yamasaki-555, 2025-01-30:
・RPI <-> STM32間の通信はCANである必要はないのでは？
　・PC間の通信は多くのNodeがあるわけではないので、CANの利点はほぼ無い。通信量も多くないから。
　・USBのほうが良いのでは？
・STM32、片足ずつよりも、そこそこ強い処理のSTM32一台でやったほうが良いのでは？
　・通信も減らせるし、良い。
・STM32も、モータと同じ通信網に入れてしまえば良いのでは？
　・ただ、電源が違う。ので、全部絶縁すれば実現できるだろう。
・RPIもモータとの通信網に入れたほうが良いのでは？
　・ログも取りやすいし。

Yusuke-Yamasaki-555, 2025-01-30:
使用予定のバッテリーの性能

- Logic Supply
  - [HRB 6000mAh 11.1V 3S 50C リポバッテリー](https://www.amazon.co.jp/-/en/HRB-Lipo%E3%83%90%E3%83%83%E3%83%86%E3%83%AA%E3%83%BC22-2V-3300mAh-6S%E5%85%85%E9%9B%BB%E5%BC%8F%E3%82%A2%E3%83%BC%E3%82%AF%E3%83%90%E3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)
    - 容量：6000mAh
    - 放電レート：50C
    - 最大バースト放電レート：100C
    - 電圧：11.1V
    - 重量：419g
- Power Supply
  - [HRB 6S 22.2V 3300mAh 60C RC充電式リポ電池](https://www.amazon.co.jp/-/en/HRB-Lipo%E3%83%90%E3%83%83%E3%83%86%E3%83%AA%E3%83%BC22-2V-3300mAh-6S%E5%85%85%E9%9B%BB%E5%BC%8F%E3%82%A2%E3%83%BC%E3%82%AF%E3%83%90%E3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) * 2
    - 容量：3300mAh
    - 連続放電率：60C
    - バーストレート：120C
    - 電圧：22.2V
    - 重量：467g

目標の定常消費電流（定常トルク時のモータ消費電流）
- 42A = 7A * 6個

目標消費電流時の連続稼働時間
- 4.7min ~= 4min42sec ~= (3.3Ah * 60) / 42A

膝以外のモータの必要トルクを下げるべき。
膝のモータの必要トルクも、できるだけ低いとありがたい。

Closed 2025-03-22.

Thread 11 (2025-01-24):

ソフトウェア構成の検討および技術検証

Yusuke-Yamasaki-555, 2025-01-24:
コンピュータの役割分担に関する検討と、技術検証

main-pc: raspberry pi 5 8gb
sub(right-leg): stm32f303k8
sub(left-leg): stm32f303k8

予定：
main -> 上位レイヤ（目標値の司令）、リアルタイム性はあまり要らない？（IMUを持たない場合？）
sub-R -> 右脚の低レイヤの制御、リアルタイム性が必要
sub-L -> 左脚の低レイヤの制御、リアルタイム性が必要

yasuohayashibara, 2025-01-25:
経緯は分からない中での意見となりますが，分散させないほうが良いかもしれません．
歩行パターンがstmで生成できるのであれば，stmを入れることで歩行を安定させることができるかもしれませんが，stmで深層学習の計算をするのは難しいと思いますので，単なる信号変換器としての役割しか持たせられないかもしれません．

Yusuke-Yamasaki-555, 2025-01-25:
ありがとうございます。

仰る通り、学習を用いる場合はstm32を使わない方が良いと考えています。
強化学習で歩行させるなら、stmを使わずに、ラズパイ5に公式のaiキットを載せるかjetsonを載せるべきだと考えています。

しかし現状はモデルベースで制御することを考えているので、このような構成を選択しています。
点設置なのでモデルベース制御だと難易度が高いことは把握していますが、強化学習でsim2realを進めるよりかは知見がありますし、パラレルリンクはurdfに対応していない点などから、実現難易度は“多少は”低いのかなと想定しています。

先生は、既存のモデルベースとsim2real、どちらの方が実現可能性が高いとお考えでしょうか。

yasuohayashibara, 2025-01-25:
モデルベースで行うことは考えていませんでした．
実現可能性ということではどちらもハードルは高いとは思います．
強いて言えばどちらが慣れているかということですね．
私は強化学習の方が慣れているので，そちらの方が早いと思いますが，モデルベースに慣れているとしたらそちらの方が早いかもしれません．
ちなみに，モデルベースの計算はそれなりにCPUの能力を要求すると思いますのでRaspberry PIで行う気がします．

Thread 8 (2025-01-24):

二足歩行シミュレーションの記録

HarukiOgawa1, 2025-01-24:
https://github.com/open-rdc/Bipedal_Robot_Hardware/issues/6 と内容は同じだが，報酬関数やどこのパラメータを変更した際に歩行がどのように変化するか記録する．

HarukiOgawa1, 2025-01-25:
## 検証することのリスト
### IsaacLab

- [ ] ロボットモデルの質量（リンク）を半分にする
- [ ] 脚以外にあたるとペナルティ（足先が地面にあたる部分）
- [ ] **URDFで可動範囲の制限をする**

### Genesis

- [ ] IsaacLabの環境を再現する　具体的に足を上げる時間の報酬関数の追加

### 検証してよかったパラメータとかのメモ

HarukiOgawa1, 2025-01-27:
可動範囲を制限して学習
詳細は後で報告します
https://github.com/user-attachments/assets/7b9f46dd-ec08-4a4b-a908-d8226d3a7d18

HarukiOgawa1, 2025-01-27:
https://github.com/open-rdc/IsaacLab/commit/6deef55277840da965338934f9f77fe27fa946c1

https://github.com/user-attachments/assets/6394ab89-7fac-464c-8016-595d2a7a55cb

HarukiOgawa1, 2025-01-28:
https://github.com/open-rdc/Bipedal_Robot_Hardware/issues/8#issuecomment-2616378459 のrevoluteの問題の解決
変換するコマンドの **--merge-joints** を除けばfixedが機能することがわかった．
```
./isaaclab.sh -p source/standalone/tools/convert_urdf.py \
  your_urdf_directory/your_urdf_name.urdf \
  source/extensions/omni.isaac.lab_assets/data/Robots/ANYbotics/your_usd_name.usd \
  --merge-joints \
  --make-instanceable
```

HarukiOgawa1, 2025-01-30:
報酬関数のdof_pos_limitsのweightを-1.0から-5.0に変更した．
膝関節が1回転するような挙動は減った．

https://github.com/user-attachments/assets/e4e627fc-90a0-4561-a0a5-594d618dcd7c

HarukiOgawa1, 2025-04-16:
https://github.com/open-rdc/Bipedal_Robot_Hardware/issues/37 のissueでロボットモデルが歩行動作を獲得できたため閉じる．

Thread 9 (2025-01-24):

回路v1.-の詳細設計および改良

Yusuke-Yamasaki-555, 2025-01-24:
回路（システム）図のversion 1.1を決めた。
配線や基板設計などの詳細な設計はまだなので、それを行う。

fig: circuit v1.1

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

sheet: main parts list v1.1
https://docs.google.com/spreadsheets/d/1lJcXPqMS-PpS88h2CHwjywfNJw795AIvWntSnHbxz7g/edit?usp=sharing

- [ ] 各部品の配置
- [ ] 配線の選定
- [ ] プルアップ抵抗やダイオード、ツェナーダイオードの選定
- [ ] 電源基板の設計
- [ ] その他基板が必要なら設計

なお、以下のissueで見つかった問題点や改善点を取り入れて行くことが考えられるため、構成もv1.1から変わっていくだろう。
[回路v1.1の検証](https://github.com/open-rdc/Bipedal_Robot_Hardware/issues/10)

Yusuke-Yamasaki-555, 2025-01-26:
基板が必要になる。
kicadで基板設計: https://www.zep.co.jp/nbeppu/article/z-kicad-da1/

Yusuke-Yamasaki-555, 2025-01-30:
回路Version1.2

電源周り以外の、Logicの通信および処理の回路をUpdate。
・コンピュータ間通信の手法は未決定。USBか、CANか、EtherCAT？
　・USBが有力。方法は調べていないが。
　・あるいは、どちらも回路上に載せて、SPIとかUARTとかI2Cとか？

電源周りは、望月氏にお願いするか、自分らで変更する予定。

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

Yusuke-Yamasaki-555, 2025-02-03:
logic周りの回路を起こしている途中

以下、logic supply周り

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

後は、CANトランシーバ周りを組めばOKなはず。それが終わり次第、footprintの方を。
CANトランシーバ周りはデータシートに沿って進める予定。
結構複雑っぽいので、できる限り同じにする方針で。
ISOW1044: https://www.ti.com/product/ja-jp/ISOW1044
ISOW1044 datasheet: https://www.ti.com/jp/lit/ds/symlink/isow1044.pdf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

Yusuke-Yamasaki-555, 2025-02-05:
Logic周りの回路図を書いた。
ISOW1044（CANトランシーバ）周りの回路はデータシートのまま。

電源回りは上のコメントと同じ

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

次は、これをフットプリントに起こす作業に入る。
コンデンサや抵抗、フェライトビーズ、自作のシンボルにはフットプリントがないので、それを作る、あるいは流用する必要がある。

yasuohayashibara, 2025-02-05:
表面実装だと思いますが，製造は外注しますか？
外注する場合は，部品の選択肢が限られるかもしれません．
詳しい人がいるので大丈夫ですかね．

Yusuke-Yamasaki-555, 2025-02-06:
製造はできれば自分たちで行おうと考えています。
望月くんと藤野くんが特論で表面実装を行っていたはずですし、ヒートガンもあったと思うので、可能であると考えています。

yasuohayashibara, 2025-02-06:
この回路で複数のデカップリングコンデンサ（C2_10uF、C3_1uF）が使われている理由は、異なる周波数成分のノイズを効果的に抑えるためです。

デカップリングコンデンサの役割
デカップリングコンデンサ（バイパスコンデンサとも呼ばれます）は、電源の安定化とノイズ除去を目的として配置されます。主な理由は以下のとおりです。

広帯域のノイズ除去

大容量（10uF）コンデンサ: 低周波ノイズを吸収します。大容量のコンデンサは比較的ゆっくりと電荷を蓄え、電源ラインの大きな電圧変動を安定させるのに役立ちます。
小容量（1uF）コンデンサ: 高周波ノイズを吸収します。小さなコンデンサは応答速度が速いため、スイッチング回路や高速デジタル信号によって発生する高周波ノイズを抑えるのに適しています。
インピーダンス低減

異なる容量のコンデンサを並列に配置することで、より広い周波数帯域にわたって低いインピーダンスを実現できます。これは、電源ラインの急激な電圧変動に対する応答を向上させるために重要です。
ICの安定動作

高速なデジタルICやマイクロコントローラでは、スイッチング動作により急激な電流変化が発生します。その際、電源ラインに瞬間的な電圧降下が起こるため、近くにデカップリングコンデンサを配置することで電圧の安定性を確保します。
結論
この回路では、10uFと1uFのデカップリングコンデンサを並列に配置することで、広い周波数帯域のノイズを効果的に除去し、電源の安定性を向上させています。これは一般的な設計手法であり、特にデジタル回路や電源系統の安定化において重要です。

Yusuke-Yamasaki-555, 2025-02-08:
ただ動かせるだけの、仮のモータ側の電源回路に使う部品の選定

https://docs.google.com/spreadsheets/d/1lJcXPqMS-PpS88h2CHwjywfNJw795AIvWntSnHbxz7g/edit?usp=sharing

yasuohayashibara, 2025-02-22:
見た感じよくできていると思います．
以下気になった点

１）シルクがはみ出している．
　　ぎりぎりも断られることがあるので注意

２）ギャップが狭そうなところがある．
　　メーカのルールに従って自動的にチェックしてくれる機能があるので，それを通した方が良い．
　　Eagleだとあります．KiCADで確認していませんが．．．

これは現時点で特に気にする必要はないと思いますが，

３）できるだけ角を作らない方が良いそうです．
　　メニューに選択肢があれば入れたほうが良いかもしれません．
　　体験実習用の基板にはTearを入れてあります．

最後に，線の太さにメリハリがありますが，電流を意識してのことですよね．

Yusuke-Yamasaki-555, 2025-02-22:
ご指摘いただきありがとうございます。

線の太さに関しては、ご指摘の通り電流を多く流しても大丈夫なように太くしてあります。
ただ仕様上500、600mAも流れることはないので、少し過剰に入れてはいます。

Yusuke-Yamasaki-555, 2025-03-01:
Logic基板を作った。
検査や見積もりはまだしていない。
回路図の書き方やPCBでのシルクとか、そこらへんは感覚でやっているので良くない。

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

yasuohayashibara, 2025-03-02:
雰囲気的には良さそうな気がしますが，配線が少ないのですね．
ベタグラウンドにはしない？
あと，誰かチェックできる方がいればチェックしたほうが良いと思います．
自分の勉強にもなりますので．

Yusuke-Yamasaki-555, 2025-03-07:
ベタGNDにするのを忘れていました。
また、回路の方を望月君からアドバイスを頂くことができたので、改良あるいは望月君が作った回路の微調整で対応する予定です。

Yusuke-Yamasaki-555, 2025-03-07:
モータへの電源供給を行うPower側の回路図Version1.3

ヒューズ（電流容量80[A]ぐらいのやつ？）を入れたい気分。
・ロードスイッチを入れて、電圧をなだらかに上げるようにすることで突入電流を抑えたほうが良い、というアドバイスを頂いている。

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

Yusuke-Yamasaki-555, 2025-03-11:
Logic回路のVersion２
* 望月君が私と並行して作ってくれた回路をベースとして、私が仕様に合わせてほんの少しだけ手を入れた回路となっている。
* Version１と比較して望月君が作っているので、ノイズ対策や利用容易性など、入門者の私が考慮できていない多くの部分が対策されている。

Version１をUpdateしなかった理由
1. 望月君にアドバイスを多くもらい、追加の部品など、変更の必要な点が多く出た。
2. 望月君が参考となる回路を作ってくれたので、Version１をアドバイス通りにUpdateすると望月君の回路に近づくことになる。
3. 時間的制約や信頼性から考えて、望月君の回路をベースとして進めたほうが良いと判断した。

「学び」という点においては、Version１を作った＋アドバイスをもらえたことで多くの学びと経験が得られたと考えている。
もちろん、Version１を改良していくのが一番学びが大きいだろうが、そこは制約との兼ね合いを考えた。
このVersion2でも運用していく中で問題が発生するかもしれないし、発生しなくても運用に関係するところでも学びが得られるだろう。

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

これをもう一度確認してもらって、JLCPCBに見積もり・発注を投げようと思う。

Yusuke-Yamasaki-555, 2025-03-11:
あと、使う部品をすべて把握しているわけではないので、そこはリスト化するときに確認する。
それほどVersion１と違いはないので、金額的に大きく変化することはないだろう。

Yusuke-Yamasaki-555, 2025-03-11:
パワー回路に含まれる、Relay Switch & Surge Killer Moduleの回路図を組んでみた。
各パーツの仕様とかはまだ選定していないし、抵抗値とかの決め方がわからんので一旦未入力。
- E-Button部分とか大体はLogicSupplyの回路のスイッチ部分と同じなので、コピーしても良いかも？

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

Yusuke-Yamasaki-555, 2025-03-14:
V2、ビアをたくさん打った。
望月君にまた見てもらった結果、まあ一旦、作ってみようという段階になったと判断。
パーツ一覧をリストアップしたら、見積もりおよび発注をしてみようと思う。

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

なお、パワー回路のほうは色々アドバイスをもらって、望月君提案のNMOSを使った回路に変える予定。部品選定はやる。

Yusuke-Yamasaki-555, 2025-03-22:
Version2の基板は完成。以下、そのCommit。
部品と基板の発注も完了した。
なので、このIssueは完遂したとしてCloseする。
なお、Power側のRelayのスイッチおよびE-Buttonの基板は以下のIssueで進める。
["https://github.com/open-rdc/Bipedal_Robot_Hardware/issues/17"](https://github.com/open-rdc/Bipedal_Robot_Hardware/issues/17)
Version2の基板の製造（？、あるいは組み立て？）は以下のIssueで進める。
["https://github.com/open-rdc/Bipedal_Robot_Hardware/issues/36"](https://github.com/open-rdc/Bipedal_Robot_Hardware/issues/36)

Closed 2025-03-22.

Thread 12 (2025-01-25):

私の持つ考えの文書化

Yusuke-Yamasaki-555, 2025-01-25:
意思疎通および認識の一致のために、現在の私の脳内にある思考を文書化して共有することを行う。

雑多に書いたあとに、GPTとかに整理してもらえば良いと思う。

Yusuke-Yamasaki-555, 2025-01-28:
https://docs.google.com/document/d/1MFqZ8LLJWyYkuHEj42IUZWVC6qOVpW08HpzFvMh-Azk/edit?tab=t.0

Closed 2025-01-28.

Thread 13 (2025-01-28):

胴体および回路搭載部分の追加

Yusuke-Yamasaki-555, 2025-01-28:

tomoki057, 2025-01-30:
胴体周りの設計を追加したものをレポジトリにプッシュしました. (Assembly6.zip)

脚部と胴体の接続部分の安全率を確かめた.

- 三角形の板を胴体の支えにしたとき

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

安全率は高いが, 板をネジで固定するのではなく溶接で固定するような設計になってしまった.

- 3本の棒を胴体の支えにしたとき

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

左右の棒の直径はΦ5mm, 真ん中の棒の直径はΦ10mmとなっている.
棒の付け根の部分の安全率が低くなっていることが確認できた.

yasuohayashibara, 2025-02-01:
@tomoki057
こちら有限要素解析の結果もアップロードされていますか？
（ファイルサイズが大きいので，GitHubには向かないかもしれませんが．．．）
できれば確認したいと思います．

tomoki057, 2025-02-01:
@yasuohayashibara
有限要素解析の結果はアップロードできていません.
有限要素解析について十分な知識がないため, 調べてから明日までにアップロードできるよう努めたいと思います.

yasuohayashibara, 2025-02-01:
サイズが大きくなるので，google driveのほうが良いかもしれません．

Yusuke-Yamasaki-555, 2025-05-06:
@akitonoguchi
時間があるときに胴体の進捗状況を本Issueに挙げていただきたいですー。

Yusuke-Yamasaki-555, 2025-05-09:
胴体の重量(想定)(最低)
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

Yusuke-Yamasaki-555, 2025-05-09:
power回路
配置案
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

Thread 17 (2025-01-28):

Power側回路の設計

Yusuke-Yamasaki-555, 2025-01-28:

Yusuke-Yamasaki-555, 2025-03-22:
リレーのスイッチおよびE-Buttonの回路を設計した。

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

commit:
[https://github.com/open-rdc/Bipedal_Robot_Hardware/tree/1eeab83b15f99a6530ec97f26e48343e742290d3](https://github.com/open-rdc/Bipedal_Robot_Hardware/tree/1eeab83b15f99a6530ec97f26e48343e742290d3)

Yusuke-Yamasaki-555, 2025-03-25:
望月君にアドバイスをもらった。
- XT60, XAは横づけで大丈夫？置く場所ある？　＝＞　問題なし。制御盤（回路ボックス）は余裕が見込まれるので。
- VH、振動で外れやすいかも。　＝＞　XHの3ピンに変更。２ピンだとXAと誤接続もあり得るので、３ピンにした。
- R1は100Ωぐらいの小さいやつのほうが応答性が良くなる。　＝＞　指摘通りに変更。
- NMOS、振動や接触を考えると、寝かせたほうが良い。金属疲労で折れる可能性。　＝＞　制御盤の高さは余裕があるだろう。もし必要ならねじ側に折り曲げる予定。

回路図：

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

PCBおよび3D：

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

おおよそできたので、これで発注する予定。

Yusuke-Yamasaki-555, 2025-04-08:
Power側回路の回路図と部品表を作成した。
専門家に目を通してもらってから発注をかける予定。

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

[2024年度humanoid_robot_発注リスト - 部品リスト（Power）.csv](https://github.com/user-attachments/files/19651409/2024.humanoid_robot_.-.Power.csv)

Yusuke-Yamasaki-555, 2025-05-02:
発注完了。

CANのデイジーチェーンに関しては、他基板を作って対応することに変更。

設計は終わったので、Closeする

Closed 2025-05-02.

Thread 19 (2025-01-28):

CANトランシーバの検証

Yusuke-Yamasaki-555, 2025-01-28:

Yusuke-Yamasaki-555, 2025-04-18:
https://www.ti.com/product/ja-jp/ISOW1044

CANトランシーバは、ISOW1044を使用。実装済み

Yusuke-Yamasaki-555, 2025-04-19:
https://github.com/open-rdc/Bipedal_Robot_Hardware/issues/39#issuecomment-2816654281

Yusuke-Yamasaki-555, 2025-04-19:
遭遇した問題（というよりも隠れた仕様）
https://github.com/open-rdc/Bipedal_Robot_Hardware/issues/39#issuecomment-2816657674

Yusuke-Yamasaki-555, 2025-05-02:
https://github.com/open-rdc/Bipedal_Robot_Hardware/issues/41
親Issueが完了した。CANトランシーバは問題なく使える。Classic CANで問題なし。

Closed 2025-05-02.

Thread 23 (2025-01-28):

ソフトウェア構成の詳細設計

Yusuke-Yamasaki-555, 2025-01-28:

Yusuke-Yamasaki-555, 2025-05-13:
歩行制御ソフトウェアのベースは俺の[ROS2_Walking_Pattern_Generator](https://github.com/open-rdc/ROS2_Walking_Pattern_Generator/tree/rdc_bipedal)を使うことを前提に進めたい。

Yusuke-Yamasaki-555, 2025-05-29:
起動手順、fsp, wpg, wsc
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

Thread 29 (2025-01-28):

CAEを用いた安全率の評価と材料の選定

Yusuke-Yamasaki-555, 2025-01-28:

Yusuke-Yamasaki-555, 2025-02-03:
inventorで構造解析、有限要素解析の話

https://www.autodesk.com/jp/campaigns/inventor-tutorials-beginner?wchannelid=8wso1h37oh#video-title

https://www.cadjapan.com/special/autodesk-concierge/useful/article/250127-01/

https://help.autodesk.com/view/NINCAD/2024/JPN/?guid=GUID-B63CD966-5467-45A2-BACA-1408418997D0

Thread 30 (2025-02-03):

nucleo-stm32 で odrive を使う検証

Yusuke-Yamasaki-555, 2025-02-03:
stm32がmaster、8108-8がnodeで、odriveを使ってcan通信をしたい。

正式には対応していないので、odrivearduinoとかを参考にしながらstm32の方にodrivetoolの必要な機能を実装する必要がある。

stm32duino + odrivearduino ができれば一番ラクだと思う。が、事例が見当たらないので、できないんじゃない？
そもそも、stm32duinoでcanが行けるのかわからん。

参考になるかもしれないurl一覧（メモ）
[stm32 odrive]
https://qiita.com/MMM-lab/items/f2773860aa9393e02e12
https://note.com/kuribata/n/n16dbbdb8978f
https://www.st.com/ja/development-tools/stm32cubeprog.html#get-software
https://[raw.githubusercontent.com/stm32duino/BoardManagerFiles/refs/heads/main/package_stmicroelectronics_index.json](https://raw.githubusercontent.com/stm32duino/BoardManagerFiles/refs/heads/main/package_stmicroelectronics_index.json)
https://github.com/stm32duino/Arduino_Core_STM32
https://www.google.com/search?client=firefox-b-e&q=odrivearduino+stm32
https://www.google.com/search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
https://discourse.odriverobotics.com/t/how-to-communicate-between-odrive-v3-6-and-stm32-nucleo-using-uart/12200
https://discourse.odriverobotics.com/t/running-odrive-fw-on-stm32f446-nucleo-just-for-fun/2306
https://github.com/uwrobotics/MarsRoverFirmware/issues/450
https://github.com/uwrobotics/uwrt_mars_rover_hw_bridge/tree/87af5b5b44f1e08cc62073173d29526009ddc7f2
https://discourse-odriverobotics-com.translate.goog/t/o-drive-v3-6-not-recognised-by-usb-in-run-mode/9518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
https://discourse.odriverobotics.com/t/porting-to-cheaper-stm32f401-possible/4320
https://discourse.odriverobotics.com/t/how-to-control-odrive-via-uart-stm32/10222
https://discourse.odriverobotics.com/t/controlling-odrive-with-stm32-board-and-matlab/12090
https://docs.odriverobotics.com/v/latest/guides/getting-started.html
https://docs.odriverobotics.com/v/latest/interfaces/odrivetool.html

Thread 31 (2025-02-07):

SteadyWin GIM8108-8 CAN-IDの割り当てをまとめる

HarukiOgawa1, 2025-02-07:
SteadyWin GIM8108-8の取扱説明書にCAN IDや使用方法について記述されているが，日本語訳がないため．また，今後の開発でCANを扱う際に確認できるようにまとめる．
https://steadywin.cn/pd.jsp?id=134&fromColId=0#_pp=0_629_3

HarukiOgawa1, 2025-03-06:
https://docs.odriverobotics.com/v/latest/manual/can-protocol.html#can-msg-address

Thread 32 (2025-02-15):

モックによる機構や構造の確認

HarukiOgawa1, 2025-02-15:
3D プリンターを用いてハードウェア（脚部）の試作品を作成して機構や構造の確認を行う．
フィラメントはASA．

印刷するCAD
https://github.com/open-rdc/Bipedal_Robot_Hardware/blob/Hardware_sub/A.zip

250215

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

HarukiOgawa1, 2025-02-15:
以下，印刷完了の部品

- [ ] BR_parts_03
- [ ] bearing_MF14mm
- [ ] BR_parts_04
- [ ] BR_parts_08(1)
- [ ] BR_parts_08(2)
- [ ] BR_parts_10

tomoki057, 2025-02-16:
お疲れ様です.
印刷する部品の数は片足1つにつき以下の数で印刷しようと考えています.
BR_parts_01: 1
BR_parts_02: 1
BR_parts_03: 1
BR_parts_04_2: 1
BR_parts_06: 1
BR_parts_07: 1
BR_parts_08(1): 2
BR_parts_08(2): 1
BR_parts_10: 2
bearing_MF14mm: 4

BR_parts_04は設計を変更する前の状態で送信してしまったため, 前回送信した部品は印刷しないでください.
申し訳ありません.

HarukiOgawa1, 2025-02-16:
了解です．ありがとうございます．
まだBR_parts_04は印刷できていないので大丈夫です．

tomoki057, 2025-02-20:
250220

3Dプリンタで印刷した部品(2/18)

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

tomoki057, 2025-02-20:
250220

inventor CAD 全体アセンブリ
https://github.com/open-rdc/Bipedal_Robot_Hardware/blob/Hardware_sub/Assembly8.iam

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

- CADとの相違点
   - 研究室の3Dプリンタで印刷した部品の穴の直径が0.3~0.4mmほど縮小してしまっていたため, M3のネジがやすりで削らないと入らなかった.

-  モックアップの設計から得られた改善点
   - BR_parts_02, BR_parts_03, BR_parts_04の回転軸につけるヒンジピンの固定方法

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

   - 膝周りの挟み込みをしないような形状にする
      - リンク機構の回転角度の範囲が歩行する際に最低限どれくらい必要なのか計算をして求めたい

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

      -  ひざ下の設計を変更. 回転軸と接地点を1直線状に配置に変更
      - 変更前

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

      - 変更後

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

Closed 2025-02-24.

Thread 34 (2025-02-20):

ハードウェア設計

tomoki057, 2025-02-20:

tomoki057, 2025-02-20:
@yasuohayashibara
設計に関してのコメントを頂きたいと思います.
お時間よろしければご対応よろしくお願いします.

inventor CAD 2024
アセンブリファイルは以下のzipファイルにまとめました.
https://github.com/open-rdc/Bipedal_Robot_Hardware/blob/Hardware_sub/Assembly9.zip

- Assembly9
   -片足のアセンブリ

- Assembly9_overall
   -胴体を含めたロボット全体

tomoki057, 2025-02-20:
- 片足

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

- 全体

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

yasuohayashibara, 2025-02-24:
いくつか不足する部品があるようです．

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

yasuohayashibara, 2025-02-25:
@tomoki057
できるだけGitHubで議論したほうが良いと思います．

> ベアリングは
内径8mm
外形14mm
幅4mm
を使おうと思っています

MF148ZZ
https://www.oss.nsk.com/jp/products/bearings/ball-bearings/deep-groove-ball-bearings/extra-small-ball-bearings-and-miniature-ball-bearings-metric-series-with-flamge/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

本定格荷重</h3>
Cr | 900 | N | 基本動定格荷重
-- | -- | -- | --
C0r | 385 | N | 基本静定格荷重

モータも900Nなので，これで良いかもしれないが，モータの方が静荷重だとまずはこちらが壊れることになる．
https://www.steadywin.cn/en/pd.jsp?id=133&fromColId=0#_pp=0_756_3

ちなみに，ロボットの重量が10kgとすると10Gが加わると10*9.8*10=980Nとなり，定格を超えます．
２個のベアリングに均等に力が加わるとしたら，20GまではOKですが．．．

ちなみに，こちら転倒実験を行った実験ですが，最大140G加わっています．
https://drive.google.com/file/d/16eoQAUiJVkXsW0Tji2VhTpSoh2EFlTJw/view

どちらにしても，モータの制限もあるので，荒く扱っても壊れないようにするためには，本体重量を下げることが望ましいです．

HarukiOgawa1, 2025-02-27:
meviusのモータ　[T-Motor AK70-10](https://www.cubemars.com/jp/goods-1031-AK7010.html)
基本定格動荷重C N　2000
基本定格静荷重C0 N　2520

GIM8108-8　https://steadywin.cn/en/pd.jsp?id=133
最大軸方向荷重 225[N]
最大ラジアル荷重 900[N]
静か動かはわからない

yasuohayashibara, 2025-02-27:
なるほど．この差は大きいですね．

HarukiOgawa1, 2025-02-27:
あと，以下[mevius](https://github.com/haraduka/mevius)で採用されているベアリングの基本定格荷重です．
Needle Bearing	[RNAF6138N](https://jp.misumi-ec.com/vona2/detail/221005155494/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)
回転数(rpm)75000
基本定格荷重 動定格(Ca)(N)2700
基本定格荷重 静定格(Coa)(N)2320

Ball Bearing	[C-B628ZZ](https://jp.misumi-ec.com/vona2/detail/110300107560/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)
基本定格荷重 Cr(動)(N)	4000
基本定格荷重 Cor(静)(N)	1590
許容回転数(rpm)	28000

tomoki057, 2025-03-04:
@yasuohayashibara
前回いただいたコメントから, いくつか修正を行いました.
確認よろしくお願いいたします.

1) ベアリングの変更

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

- リンクに付けるベアリング (上)

https://www.monotaro.com/p/0032/9637/?t.q=628zz

- 膝に付けるベアリング (下)

https://www.monotaro.com/p/3840/1246/?srsltid=AfmBOopN_z4wnQSrpLZrMbkSpYNaax543b9P3Kl2RTWv4OUV-_zPsolg

2) 隙間を埋める部分の部品の追加

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

- 厚さ1mmのシムリングを追加

https://www.monotaro.com/p/3476/5175/

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

膝部分の隙間の厚さが小数点を含むため, ここの部品は3Dプリンタで印刷しようと考えています.

3) ひざ下の設計の変更

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

接続部分の面積を増やしました

4) スペーサの追加

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

- 六角スペーサ
https://www.monotaro.com/p/0106/6686/?srsltid=AfmBOopaTB5CTF6veg8FyMZ961DDBlanq0Ftg6N3GjN52-_dOJTnC7Mg

ネジで締結する際に円柱だと中のスペーサが空回ってしまうのではないかと思ったため, 六角のスペーサにしました.

4) 公差

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

- ヒンジピン
https://jp.misumi-ec.com/vona2/detail/110300099520/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

全体的に公差の考慮が必要な部分は0.2mmほど穴を広げました

yasuohayashibara, 2025-03-05:
@tomoki057
反応遅れましたが，CADデータを拝見させていただければと思います．

tomoki057, 2025-03-06:
@yasuohayashibara

確認よろしくお願いします.
https://github.com/open-rdc/Bipedal_Robot_Hardware/blob/Hardware_sub/20250306.zip

yasuohayashibara, 2025-03-10:
回答が遅くなり申し訳ありません．

１）ファイルが不足しています．
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

２）価格的にあまり変化がなければ気にしなくても良いですが，ザグリを入れなくても良い部分です．
矢印でいくつか示していますが全てです．
（おそらく他にもあると思いますが，干渉が問題になる部分以外は不要だと思います．）
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

３）この隙間は電子回路部品に対して最適？
電子部品と干渉しない幅で，できるだけ狭いほうが良いです．
電子部品も図面にいれると良いかなと思います．
※実物があるので，追加できると思います．
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

４）こちらの部品は六角形の方が良いが，入らない場合追加工ができないので，余裕を持った寸法にした方が良い．
中で回転しないことを考えると，丸より六角の方が良いが，丸はサイズが小さい時に追加工で対応できるが，六角は対応できないので，余裕を持った寸法にした方が良い．
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

tomoki057, 2025-03-25:
@yasuohayashibara

部品の見積もり料金をmeviyとJLC3DPで比較したところ, JLC3DPの方がmeviyよりも料金が半分程安くなったため, 発注をJLC3DPでお願いしようと考えているのですが, JLC3DPの切削の精度が少し心配です.
JLC3DPでも精度的なところは大丈夫かどうか教えていただきたいです.

部品見積表(簡易的)
https://docs.google.com/spreadsheets/d/1W02CFEZUhgf_ZYfZ93xlnMxTkhgzjHgARCEtxRBruv8/edit?usp=sharing

yasuohayashibara, 2025-03-26:
JLC3DPは私自身は使用したことがないため，分かりません．
なお，公差が指定できるものに関しては，指定した公差を満たさない場合は返品できます．
（メーカも確認してから出荷すると思います．）

meivyも公差を指定しないと普通公差などで加工されると思いますのでご注意下さい．
（公差の指定の仕方で価格がだいぶ変動するという話は聞いたことがあります．）

重要なのは，必要となる公差を把握することです．
これに関しては個別に相談していただければと思います．

tomoki057, 2025-04-08:
@yasuohayashibara

https://github.com/open-rdc/Bipedal_Robot_Hardware/blob/Hardware_sub/20250402.zip

片足のみのアセンブリになります.ファイル名は20250401(L)になっています.
確認よろしくお願いします.

yasuohayashibara, 2025-04-13:
回答が遅くなり申し訳ありません．

まず，いくつか部品が足りないようです．
不完全な状況でのチェックなので，見当違いの指摘もあるかもしれません．

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

１）干渉がある．
これは上記の問題が関係しているかもしれませんが，干渉しています．
ただし，向きや位置を修正すれば治るところなので，これによるメカの修正は不要だと思います．

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

２）ザグリ＋六角レンチを通す穴
上記の干渉のチェックで見つけましたが，ピンが干渉しています．
緑矢印の右の部品はザグってあり，左の部品はザグっていないので，おそらくザグリを入れる方が逆になっています．
ギャップを見るとピンの方向はこちらで正解ですので，緑の部品側で干渉しないように調整することが必要だと思います．
またこのギャップでは六角レンチが通らないので赤の部分に予めレンチ用の穴を明けておいたほうが良いと思います．
安全性の観点から指が入らない程度の穴にしたほうが良いと思います．

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

３）組立時の問題
同じ組み立ての問題で，こちらは裏側に六角レンチを入れる隙間が無く，おそらくレンチ用の穴もあけられないので，締め付けができないと思います．
この場合，ピンの向きを入れ替えたほうが良いです．
下の図の矢印の部分にタップを立てても良いですが十分な強度が得られるかが微妙なので，セルフクリンチングナットを入れると良い気がします．ギャップがあまりないと思いますので，セルフクリンチングフラッシュナットが良いかもしれません．

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

４）ナットの問題
回転軸にナットを使用するのは緩みが発生するおそれが高いため，あまりおすすめできません．
ただし，ピンを使用する関係で避けて通れないため，使用するナットには緩み止めが入ったものを使用してください．
ナイロンナットなどが使用できると良いですが，もしかしたらギャップの関係で使用できないかもしれません．
もしくは強めのロックタイトを使用しても良いかもしれませんが，分解するのが大変かもしれません．
あと，緩み止めの入ったナットは複数回外すと効果がなくなると思いますので，あまり取り外ししないほうが良いです．

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

tomoki057, 2025-04-14:
@yasuohayashibara

お忙しい中ご対応ありがとうございます。現時点でのハードウェアの見積もりが出来ましたので確認お願いいたします。

- スプレッドシート

https://docs.google.com/spreadsheets/d/1AoQhdShoYTbUUt8ozvRxeLYt9eYG21Pzni79hF-8NDg/edit?usp=sharing

- 発注選択画面

[JLC3DP_見積.pdf](https://github.com/user-attachments/files/19731352/JLC3DP_.pdf)

yasuohayashibara, 2025-04-14:
@tomoki057
修正箇所があったかと思いますが，すでに対応済みでしょうか？

JLC3DPについてですが，正直なところ私自身は発注経験がないため，適切かどうかの判断は難しいところです．
ある程度のリスクはあるかもしれませんが，発注してみても良いとは思います．

可能であれば，まずは一部のみ発注して様子を見るのが望ましいとは考えますが，組み立て期間が長期にわたることも踏まえ，その点はお任せします．

tomoki057, 2025-04-16:
@yasuohayashibara

スラックにて確認しましたが, 問題がなければこの内容で発注をお願いしたいです.
よろしくお願いいたします.

- zipファイル

https://github.com/open-rdc/Bipedal_Robot_Hardware/blob/Hardware_sub/20250416.zip

- スプレッドシート
https://docs.google.com/spreadsheets/d/1AoQhdShoYTbUUt8ozvRxeLYt9eYG21Pzni79hF-8NDg/edit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

- PDF

[Humanoid Robot 見積1.pdf](https://github.com/user-attachments/files/19772690/Humanoid.Robot.1.pdf)

Yusuke-Yamasaki-555, 2025-04-16:
発注に関してですが、私と小川くんから指摘がありますので、対応ができ次第でお願いします。
発注の仕方に関しては、藤野くんから共有してもらった情報を後ほど共有します。
支払い方法はPayPalあるいはクレジットカードが可能であったと思います。

tomoki057, 2025-04-21:
発注用のzip fileです.
https://github.com/open-rdc/Bipedal_Robot_Hardware/blob/Hardware_sub/20250421.zip

スプレッドシート
https://docs.google.com/spreadsheets/d/1AoQhdShoYTbUUt8ozvRxeLYt9eYG21Pzni79hF-8NDg/edit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

PDF

[Humanoid Robot 見積1.pdf](https://github.com/user-attachments/files/19829229/Humanoid.Robot.1.pdf)

yasuohayashibara, 2025-04-21:
山崎君と途中まで進めましたが，JLC3DPに関しては発注の手前で止めました．
@tomoki057 に確認してもらってから発注したいと思います．

HarukiOgawa1, 2025-04-22:
https://github.com/open-rdc/Bipedal_Robot_Hardware/issues/34#issuecomment-2817603233 の発注時にリンクパーツの材料がアルミ6000番台だった場合の解析をしてみた結果，変形する可能性があったため，7000番台に変更しました．
↓穴の外側方向に荷重30Nを加えた

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

HarukiOgawa1, 2025-05-08:
ハードウェアの発注記録はこっちにコメントをお願いします．
https://github.com/open-rdc/Bipedal_Robot_Hardware/issues/45

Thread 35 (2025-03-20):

SteadyWin GIM8108-8を位置制御で動かす

HarukiOgawa1, 2025-03-20:
SteadyWin GIM8108-8を位置制御で動かすサンプルプログラムを作成する．

HarukiOgawa1, 2025-03-21:
キーボード入力で動くプログラムはできた
https://github.com/open-rdc/Bipedal_Robot_Hardware/blob/odrive_gim8108-8/odrivetool/filtered_position_control.py

https://github.com/user-attachments/assets/f0c46cf9-26b2-4e91-8a1b-6c3ce504ca90

HarukiOgawa1, 2025-04-15:
https://github.com/open-rdc/Bipedal_Robot_Software/issues/2 に移行するためcloseする．

Closed 2025-04-15.

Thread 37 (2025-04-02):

URDF_simulation

tomoki057, 2025-04-02:

tomoki057, 2025-04-02:
20250402
URDF用のファイル
https://github.com/open-rdc/Bipedal_Robot_Hardware/blob/Hardware_sub/20250402.zip

- A_box

重量: 7263.360 g (相対誤差 = 0.000567%)
慣性モーメント:
I1: 44105918.745 g mm^2 (相対誤差 = 0.000567%)
I2: 70036319.295 g mm^2 (相対誤差 = 0.000567%)
I3: 86554397.314 g mm^2 (相対誤差 = 0.000567%)

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

- A_calf(L)

重量: 581.098 g (相対誤差 = 0.008399%)
慣性モーメント:
I1: 3005565.539 g mm^2 (相対誤差 = 0.008399%)
I2: 3394089.955 g mm^2 (相対誤差 = 0.008399%)
I3: 580175.165 g mm^2 (相対誤差 = 0.008399%)

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

- A_calf(R)

重量: 581.098 g (相対誤差 = 0.008399%)
慣性モーメント:
I1: 3005565.539 g mm^2 (相対誤差 = 0.008399%)
I2: 3394089.955 g mm^2 (相対誤差 = 0.008399%)
I3: 580175.165 g mm^2 (相対誤差 = 0.008399%)

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

- A_foot(L)

重量: 199.496 g (相対誤差 = 0.035448%)
慣性モーメント:
I1: 38569.077 g mm^2 (相対誤差 = 0.035448%)
I2: 690047.835 g mm^2 (相対誤差 = 0.035448%)
I3: 672474.784 g mm^2 (相対誤差 = 0.035448%)

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

- A_foot(R)

重量: 199.496 g (相対誤差 = 0.035448%)
慣性モーメント:
I1: 38569.077 g mm^2 (相対誤差 = 0.035448%)
I2: 690047.835 g mm^2 (相対誤差 = 0.035448%)
I3: 672474.784 g mm^2 (相対誤差 = 0.035448%)

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

- A_hip(L)

重量: 1343.828 g (相対誤差 = 0.498767%)
慣性モーメント:
I1: 1620233.675 g mm^2 (相対誤差 = 0.498767%)
I2: 2953999.479 g mm^2 (相対誤差 = 0.498767%)
I3: 3000756.260 g mm^2 (相対誤差 = 0.498767%)

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

- A_hip(R)

重量: 1463.019 g (相対誤差 = 0.502991%)
慣性モーメント:
I1: 1749718.494 g mm^2 (相対誤差 = 0.502991%)
I2: 3223385.949 g mm^2 (相対誤差 = 0.502991%)
I3: 3263127.737 g mm^2 (相対誤差 = 0.502991%)

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

Yusuke-Yamasaki-555, 2025-04-02:
ありがとうございます！
あとはこちらで引き継ぎます。

１つ質問です。
A_hipが左右で重量が大きく異なるようですが、パーツの有無や形状で異なる部分がある感じですか？

yasuohayashibara, 2025-04-03:
念のため伝えておくと，

よく知られた話ですが，URDFファイルの質量や慣性モーメントが小さすぎるとシミュレーションがうまく動作しないおそれがあります．
極端に小さな値の場合は，少し大きくしてください．
（もしくはサンプリングタイムを小さくしても解決しますが，シミュレーションの速度が下がります．）

結果にはそれほど影響しません．
（というかそれが問題になるほど精度の高いシミュレーションをするのが難しいので，そこにこだわっても得られるものが少ないです．）

Yusuke-Yamasaki-555, 2025-04-03:
parts properties

[parts_properties.txt](https://github.com/user-attachments/files/19589978/parts_properties.txt)

Yusuke-Yamasaki-555, 2025-04-03:
URDFのモデルを更新した。

寸法、質量、慣性ともに良好。

https://github.com/open-rdc/Bipedal_Robot_Software

これを学習に突っ込めばいいと思う。

@HarukiOgawa1 この状態でお渡しします。何かあれば連絡ください。

Yusuke-Yamasaki-555, 2025-04-03:
@tomoki057
モデルを作って１つ気づいた点として、重心がロボット後方にあるので後ろに転倒する挙動が見られます。
もしかしたら、胴体の箱をより前に置くように腰から上のパーツの変更をお願いするかもしれません（今からでもしてもらえたら嬉しいです）。
具体的には、胴体にあたるBoxを今の位置から40mm~50mmぐらい前にだすと重心が真ん中、あるいは前方に移動すると思います（感覚ですが）。

HarukiOgawa1, 2025-04-06:
シミュレーションはhttps://github.com/open-rdc/Bipedal_Robot_Hardware/issues/6 と同じ方法で行った．
https://github.com/open-rdc/IsaacLab/tree/rdclab_bipedal_robot

現時点では，このモデルだと定常トルクの7.5 [Nm]では歩行動作（立つことも）ができなかった．トルクの場合，13 [Nm]が最低ラインとわかった．速度は調査中だが，公称速度の11.52 [rad/s]より低い値で歩行できている．
前回と違い慣性や質量が適切に設定されたため，しっかり重心移動している．

unitree.py
effort_limit = 13[Nm], velocity_limit = 10 [rad/s], stiffness = 20, damping = 0.16
報酬関数
feet_air_time "threshold" = 0.6, self.rewards.feet_air_time.weight = 1.5
https://youtu.be/uz-I9l7IAo0

https://github.com/user-attachments/assets/8c2b3415-83a7-466b-981c-981121c68602

ーーーーー
元の報酬関数の値の場合はロボットは立って移動していたが，発振して移動していた
feet_air_time "threshold" = 0.4, self.rewards.feet_air_time.weight = 0.75
https://youtu.be/uKG5Hj4xWOE

https://github.com/user-attachments/assets/11469dac-2652-458c-940f-3ab5a4074f56

学習したパラメータリスト
https://docs.google.com/spreadsheets/d/1VbAXaOXzHfLSzCUkBw7iuE2QPG065hXWnXxo-NgM_Fo/edit?gid=0#gid=0

HarukiOgawa1, 2025-04-06:
https://github.com/open-rdc/Bipedal_Robot_Hardware/issues/37#issuecomment-2776354962 のように重心がやや後ろにあった

https://github.com/user-attachments/assets/d012c495-6692-4039-b8ca-41c9b69045bd

Yusuke-Yamasaki-555, 2025-04-07:
歩行可能かどうか、どこらへんに問題があるのかが判明した。
加えて、完了の有無にかかわらず次の作業に移行する予定であったため、本IssueをCloseする。

得るものは得られたので、Completed

Closed 2025-04-07.

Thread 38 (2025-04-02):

ボディの重量

yasuohayashibara, 2025-04-02:
#37 を見ての感想ですが，胴体の重量が7kgは重いと感じました．
制御的には重心は高いほうが歩行はしやすくなるのですが，モータのトルクが不足するかもしれないので，削れるところは削っておいたほうが良いです．
重心を高くしたい場合は後でおもりを追加することができますが，重量を削ることは難しいので常に軽量化は意識したほうが良いと思います．

共有したらissueを閉じて下さい．

HarukiOgawa1, 2025-04-06:
こちらの検証の結果，定格トルク 7.5[Nm]より5.5 [Nm]オーバーであることがわかりました．
現段階のモデル（設計）を軽量化した方が良いと思います．
https://github.com/open-rdc/Bipedal_Robot_Hardware/issues/37#issuecomment-2781361343

yasuohayashibara, 2025-04-06:
軽量化は目指したほうが良いですが，7.5Nmは常に出し続けられるトルクで大抵は熱で決まる値であるため，平均的にこのトルクになっていれば問題ありません．
ちなみに，瞬時最大トルクは22[Nm]ですが，おそらく出せるのはほんの一瞬なのでピークはその間にあると考えたほうが良いです．

Yusuke-Yamasaki-555, 2025-04-15:
共有したのでClose。

Closed 2025-04-15.

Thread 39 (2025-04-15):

Logic回路基板Version2の検査

Yusuke-Yamasaki-555, 2025-04-15:
作りながら回路の検査を行う。

Yusuke-Yamasaki-555, 2025-04-15:
## 電源周りの検査

Raspberry Pi と NUCLEO への 5[V] 供給はOK
しかし、RPIとNUCLEOのスイッチにかかわらず、５Vが供給されてしまう

### 原因
５V5Aを供給するDCDCコンバータモジュールに乗ってるDCDCコンバータ（MYMGK00506ERSR）の仕様のせい
https://www.murata.com/ja-jp/products/productdetail?partno=MYMGK00506ERSR

1. CTRLピン（ON/OFF, EN(Enable)）は、内部でプルアップされている。
2. 加えて、内部でプルダウンもついている
3. この２つの抵抗でVINが分圧されて、CTRLピンから出力されている（CTRLは入力ピンなのに！）。
4. 分圧された電圧がCTRLに流れているので、CTRLがオープンまたはHIでDCDCの電源がONになる。
5. 今の回路だと、CTRLをLOWにできる回路になっていない。
6. なので、スイッチにかかわらず常にDCDCがONになる不具合が生じている。

### 対策
DCDCコンバータの推奨回路に則り、トランジスタをつけるために、DCDCのCTRLにつながっているTBD62783Aの代わりにTBD62083Aをつける。
- COMMONは使わない。GNDが逆なので、配線で飛ばす必要がある

他、現在の状態でも、主電源のON/OFFはできる（RPI、STM個別の電源を操作はできない）ので、動きはする。
なので、現状のVersionで完成させても良い。

Yusuke-Yamasaki-555, 2025-04-18:
canトランシーバへの+5V、GNDの導通確認
次:can通信できるか

Yusuke-Yamasaki-555, 2025-04-19:
## CAN通信の調査（途中経過）

### 現状

- 実験環境：STM32 to PC (CAN to USB) 間で CAN (Classic) 通信を行う
- - 送信側：STM32
- - 受信側：PC
- 現状：できていない
- 電源の導通：仕様通り５ [V] きている
- 通信線の電圧（テスターで検査）
- - Tx: abt. 3.3 [V]
- - Rx: abt. 0 [V] (現時点では未使用)
- - H: abt. 2.8 [V]
- - L: abt. 2.8 [V]
- ビットレート：500 [kbps]

### タスク

- [ ] ：オシロスコープでTx、H、Lに信号が流れているか（データが乗っているか）確認
- [ ] ：Rxの実装も行ってみる
- [ ] ：STM32側のプログラムの再確認
- [ ] ：PC側のプログラム（コマンド）の再確認
- [ ] ：CAN to USBの変更（終端抵抗値の違いの可能性を考慮）

Yusuke-Yamasaki-555, 2025-04-19:
## CANトランシーバに関して、電源未投入時に信号を出しているTxを入力すると電源確認用のLEDが光る問題

光るLED：Power（弱く光る）、STM（普通に光る）

＝＞　結論：仕様（であろう）

### 推定されたプロセス

1. 電源未投入、基板とNUCLEOのGNDが共通になっているときに、3.3 [V] 程が流れているNUCLEOからのTx信号を入力
2. [こちらのI/O Schematics](https://www.ti.com/jp/lit/ds/symlink/isow1044.pdf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)にある構成から、CANトランシーバのV_{IO}とTXDを比較してTXDのほうが電位が高いので、V_{IO}ピンからTXDの電流が逆流（静電保護のためのクランプ回路？恐らく順電圧が結構低いダイオード）
3. DCDCコンバータのV_{OUT}ピンまで行き、そこに繋がっているSTMのLEDに流れる
4. DCDCコンバータ内を通った後、PowerのLEDに流れる

（望月くんらによる推定）

壊れないとはいえ逆流は良くないので、上記の状況にならないようにするべき

Yusuke-Yamasaki-555, 2025-04-20:
## NUCLEOへの入力電圧が足りていない問題

以下のデータシートより、NUCLEO-H755ZI-Qへの電源供給に使用しているVINピンは７V〜11Vなのに対し、入力電圧は５Vになっている。
https://www.stmcu.jp/design/document/users_manual/68524/

（勘違いしてた...）

これで正常に動くかはわからん。
作り直したほうがいいなこれ。あるいは、７Vを生成する基板を別途追加して繋げるか、他に５V入力の５V_EXTピンがあるのでそちらに飛ばすか。

Yusuke-Yamasaki-555, 2025-04-27:
## CAN1のTx, Rx逆接問題

タイトルママ。CN7のPB8, PB9に伸びているCAN1のTx, Rxが、STM32のピン配置と逆に繋がっていた。

正（ピン配置）：
- PB8: CAN1_RX
- PB9: CAN1_TX

誤（Logic回路）：
- PB8: CAN1_TX
- PB9: CAN1_RX

ここ、配線を逆にする必要がある。
なので、Logic回路Version3を組まなければならなくなった（やりようはあるけど、作り直したほうが良い）。

これに気づくまで１週間かかった。
「ここは問題ないだろう」という盲信だめ。何事にも疑ってかかり、何事も確認をすること。
https://github.com/open-rdc/Bipedal_Robot_Hardware/issues/41#issuecomment-2833274553

yasuohayashibara, 2025-04-27:
実は筒井君も，SteadyWinのモータで同じ問題にしばらく悩んでいました．
（諸事情により非公開の議論かもしれませんが．．．）
2度あることは3度あると言いますので，情報を共有して取り組むことは重要ですね．

Yusuke-Yamasaki-555, 2025-05-02:
https://github.com/open-rdc/Bipedal_Robot_Hardware/issues/41
CAN周りはOK

あとは、RPIへの電源供給のみ。

Yusuke-Yamasaki-555, 2025-05-02:
RPIへの電源供給、RPI3B+で実験した。
5V出力されていて、正常に起動した。

RPI5Bで試していないので消費電流は確認できていないが、まあちゃんと５Vが供給できている。

Yusuke-Yamasaki-555, 2025-05-02:
動画

3B+でピーク0.5~.6A消費していそうなので、これ以上を想定した方が良い

https://github.com/user-attachments/assets/32c63793-0c2d-496f-8f74-9bebbfefb6c5

Yusuke-Yamasaki-555, 2025-05-24:
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

5V_EXTにピンヘッダをつけてそこに供給してやるのが楽な構成

Closed 2025-05-02.

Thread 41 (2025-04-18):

STM32とPC間でCAN通信

Yusuke-Yamasaki-555, 2025-04-18:

Yusuke-Yamasaki-555, 2025-04-19:
https://github.com/open-rdc/Bipedal_Robot_Hardware/issues/39#issuecomment-2816654281

Yusuke-Yamasaki-555, 2025-04-20:
プログラムの問題として、FIFO/QueueがRAMに割り当てられていない。

`main.c`で`HAL_FDCAN_AddMessageToTxFifoQ()`を実行時に`== HAL_OK`とはならず、`stm32h7xx_hal_fdcan.c`の2752行目でのエラーチェックIF文に引っかかっている。
そのせいでERRORになり、データを送れていないのだと思う。

Yusuke-Yamasaki-555, 2025-04-20:
CANの話
https://www.google.com/url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
https://cdn.vector.com/cms/content/know-how/VJ/PDF/For_Beginners_CAN_CANFD.pdf

Yusuke-Yamasaki-555, 2025-04-22:
https://github.com/STMicroelectronics/STM32CubeH7/blob/master/Projects/STM32H745I-DISCO/Examples/FDCAN/FDCAN_Classic_Frame_Networking/CM7/Src/main.c
上記コードを参考に、設定周りをほぼ同じにしたら、[上記の問題](https://github.com/open-rdc/Bipedal_Robot_Hardware/issues/41#issuecomment-2816949574)が解決して、データを出力する処理が実行できるようになった。

しかし、PCには届かない。Txのメモリ領域に出力するデータを入れることはできているが、出力することができていない。
なので出力するデータがメモリ領域に溜まり、領域MAXになるとエラーを吐いてしまう。

原因としては、
- 回路が悪い
- 受け取り手が悪い（受け取り手が存在しない状態になっている可能性）
- Clockの設定が悪い

の３点が主に考えられる（気がする）。Clockは特にエラーも出ていないし、各Clockは30MHzあるいは60MHzに揃えている。
CANのビットレートは500000Mbpsで、Clockは30MHzにしている。

あるいは、state-point (だっけ？) が互いに合っていないとだめなのか？（そんなはずはないと思うが）。

yasuohayashibara, 2025-04-22:
ここらへんは行き詰まると延々と抜け出せなくなるパターンですね．
よくあるのは通信を行うために必要なフラグを立てていなかったといういうやつで，マニュアルを相当読み込まないと分からないこともあります．
動作実績のあるプログラムでハードウェアを確認して，ハードウェアに問題が無いかを確認してからソフトウェアの開発をした方が良いかもしれません．
その点では，mbedの環境が使用できる組み合わせであれば，まずはそちらでハードウェアを確認して，ソフトウェアを開発したほうが効率的かもしれません．
処理速度などに問題なければ，そのままmbedの環境を使用しても良いとも思いますが．．．

Yusuke-Yamasaki-555, 2025-04-27:
えー、CAN通信できました。
配線を間違えていたことが原因でした。

STM32を挿すピンソケットとCANトランシーバを繋ぐCAN Tx, Rxの配線が、Tx Rxを逆につないでいました。
配線、回路の問題でした。
STM32 -> CAN2USBに成功しました。

次、もう片方のCANトランシーバも試して、成功したら、今度は CAN2USB -> STM32 を試して、終わりかな。

Yusuke-Yamasaki-555, 2025-04-27:
CAN2でも成功

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

Yusuke-Yamasaki-555, 2025-04-27:
https://github.com/open-rdc/Bipedal_Robot_Hardware/issues/41#issuecomment-2816949574
この問題に関して追記。
このエラーは、`hfdcan.Init.TxFifoQueueElmtsNbr`を１に設定すれば解決する。あるいは０以外にすれば良いんでないかな。

Yusuke-Yamasaki-555, 2025-04-30:
CubeIDEのデバックモードを利用してメモリを覗いてみた感じ，Rxを受け取ってメモリ領域には書き込めていることが確認できた．しかしそれをプログラム上から読み出すことができていない．書き込めているということは割り込み処理はできているわけだけれど，割り込み処理に合わせて実行される関数の実装ができていないのかも？

Yusuke-Yamasaki-555, 2025-05-01:
いや、メモリに書き込めているのにそれをフラグとしてCallback関数が動いていないということは割り込みができていないということでは？

Yusuke-Yamasaki-555, 2025-05-01:
データの受け取りもできた。
原因は、割り込みラインの設定ができていなかった。

~.iocで設定するNVICのLineの設定に加えて、`HAL_FDCAN_ConfigInerruptLines()`でLineの設定もする必要があった。
この２箇所で、同じInterrupt Lineを指定してやる必要がある。

例：
```c
HAL_FDCAN_ConfigInterruptLines(&hfdcan2, FDCAN_IT_RX_FIFO1_NEW_MESSAGE, FDCAN_INTERRUPT_LINE1)
```

この関数で設定してやらないと、割り込み処理で参照（あるいは割り込み処理のフラグが立つ）できるInterrupt Lineはデフォルトで０に設定される。

ココらへんの説明は、stm32h7xx_hal_fdcan.c (or ~.h) に書かれている。
Search機能を使って検索すると当たる。

なぜ２箇所設定する必要があるのかは不明だが、恐らく、それぞれで設定しているシステムが違うのだと思う。
STM32H755のデータシート（RM0399）の、Fig. 775. CAN subsystem や Fig. 776. FDCAN block diagram に示されている、CAN CoreとInterrupts Interface の２つがそれぞれ該当するのかもしれない。
（データシートリンク：https://www.stmcu.jp/design/document/reference_manual/67223/）

Yusuke-Yamasaki-555, 2025-05-01:
これで、CAN2の方はTx, Rxともに動作確認ができた。
あとは、CAN1のRxを確認すれば完了。

（まあ、回路は作り直しなんですけどね。ISOW1044の動作確認や使い方がわかったということで）

Yusuke-Yamasaki-555, 2025-05-02:
CAN1のRxも確認できた。
Message RAMのアドレスがデフォルトだとCAN1とCAN2で同じなようで、CAN2のMessage RAMにオフセットをかけてやらないと行けないっぽい。
```c
hfdcan2.Init.MessageRAMOffset = 17;
```

Message RAMについては、データシート（[https://www.stmcu.jp/design/document/reference_manual/67223/](https://www.stmcu.jp/design/document/reference_manual/67223/%EF%BC%89)）の59.4.2章（p.2626）に記載されている。
今回は17bit1のオフセットをかけた。
これは、CAN1のMessage RAMのサイズが17bitであるからである。
- 11-bit filter: 1
- Rx FIFO: 16

Yusuke-Yamasaki-555, 2025-05-02:
てなわけで、このIssueで行うタスクはすべて達成された。
なので、このIssueはComplete Close。

Closed 2025-05-02.

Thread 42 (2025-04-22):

Inventor の材料設定にアルミ7000系を追加する方法

HarukiOgawa1, 2025-04-22:
ロボットのハードウェア設計はAutordesk Inventorを用いている．デフォルトの材料設定だとアルミの6000系しかないため，追加する方法をここに記載する．

HarukiOgawa1, 2025-04-22:
JLCCNCの材料
https://jlccnc.com/jp/cnc-machining#materials

HarukiOgawa1, 2025-04-22:
方法
- メニューの[ツール] > [材料]（Material）を開く
- 材料一覧の中から，近い材料のアルミ6061を選択し，右クリックで複製
- 複製の名前変更と編集で物理特性等を変更する
- 材質の参考　[CADDi Drawer A7075（超々ジュラルミン）の特徴、比較、性質について解説](https://caddi.com/drawer/library/all/all/12529/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,A7075%E3%81%AE%E7%89%B9%E5%BE%B4%E3%81%A8%E3%81%97%E3%81%A6%E3%80%81%E3%82%A2%E3%83%AB%E3%83%9F%E3%83%8B%E3%82%A6%E3%83%A0%E3%81%AE%E4%B8%AD%E3%81%A7%E6%9C%80%E3%82%82%E5%BC%B7%E5%BA%A6%E3%81%8C%E5%BC%B7%E3%81%84%E3%81%93%E3%81%A8%E3%80%81%E9%89%84%E9%8B%BC%E6%9D%90%E6%96%99%E3%81%AB%E5%AF%BE%E3%81%97%E3%81%A63%E5%88%86%E3%81%AE1%E3%81%AE%E8%BB%BD%E3%81%95%E3%81%A7%E3%81%82%E3%82%8B%E3%81%93%E3%81%A8%E3%81%8C%E6%8C%99%E3%81%92%E3%82%89%E3%81%BE%E3%81%99%E3%80%82%20%E4%B8%80%E6%96%B9%E3%81%A7%E3%80%81%E5%BF%9C%E5%8A%9B%E8%85%90%E9%A3%9F%E5%89%B2%E3%82%8C%E3%82%84%E8%80%90%E9%A3%9F%E6%80%A7%E3%81%AB%E3%81%A4%E3%81%84%E3%81%A6%E5%8A%A3%E3%81%A3%E3%81%A6%E3%81%84%E3%82%8B%E4%B8%80%E9%9D%A2%E3%82%82%E3%81%82%E3%82%8A%E3%81%BE%E3%81%99%E3%80%82%20%E3%81%9D%E3%81%AE%E3%81%9F%E3%82%81%E3%80%81%E4%BD%BF%E7%94%A8%E7%92%B0%E5%A2%83%E3%81%AB%E7%95%99%E6%84%8F%E3%81%99%E3%82%8B%E5%BF%85%E8%A6%81%E3%81%8C%E3%81%82%E3%82%8A%E3%81%BE%E3%81%99%E3%80%82)

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

HarukiOgawa1, 2025-04-22:
共有でき次第closeする．

tomoki057, 2025-04-22:
ありがとうございます.
先ほど項目入力してみたので画像を共有します.

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

HarukiOgawa1, 2025-04-29:
共有できたため，closeする

Closed 2025-04-29.

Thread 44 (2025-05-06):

リスクアセスメントの議論・実施

Yusuke-Yamasaki-555, 2025-05-06:
Discussionで決まった安全性確保のための設計を踏まえて、リスクアセスメントを実施していく。
https://github.com/open-rdc/Bipedal_Robot_Hardware/discussions/43#discussioncomment-13034817

Yusuke-Yamasaki-555, 2025-05-06:
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

Yusuke-Yamasaki-555, 2025-05-06:
リスクアセスメントの構成
1. 危険源の同定
2. リスクの見積もり・評価
3. 安全妥当性確認

Yusuke-Yamasaki-555, 2025-05-06:
豆腐型の案を適用する前に、リスクアセスメントを実施して、その対策として豆腐にするという流れのほうがきれいか？
豆腐型を先にしても良いとは思うが。

HarukiOgawa1, 2025-05-06:
基本安全規格　ISO12100
https://jp.idec.com/RD/safety/law/iso-iec/iso12100

HarukiOgawa1, 2025-05-06:
現状の状態
https://github.com/open-rdc/Bipedal_Robot_Hardware/issues/34#issuecomment-2671175747

Yusuke-Yamasaki-555, 2025-05-06:
前提条件の明確化
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

yasuohayashibara, 2025-05-06:
反応悪くて申し訳ありません．
できるだけ事前に行った方が良いと思います．
事後に行うと作り直しの手間が生じます．

Yusuke-Yamasaki-555, 2025-05-06:
承知しました。
ありがとうございます。

yasuohayashibara, 2025-05-06:
再度になりますが，こちらにリスクアセスメント関連の資料があります．

https://drive.google.com/drive/folders/1pLhzwyBzHMmgb-cA3k4Gf3PoROcyMDI3?usp=drive_link

HarukiOgawa1, 2025-05-13:
つくばチャレンジの仕様条件
https://tsukubachallenge.jp/2024/regulations/specs

Yusuke-Yamasaki-555, 2025-06-10:
2025/5/29 and 6/3: 第1回終了

次回は、安全方策の設計が終了次第決定

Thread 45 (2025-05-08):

ハードウェア(膝)の発注記録

HarukiOgawa1, 2025-05-08:
JLPCBに膝関節の発注記録を残し開発者の状況共有を行う．

HarukiOgawa1, 2025-05-08:
現在の状況確認
発注前のCADデータ
https://github.com/open-rdc/Bipedal_Robot_Hardware/issues/34#issuecomment-2817603233

メールのやり取りに関しては省略し，問題点だけ以下に残していく．
### 1. 3D CADと2D図面の穴の違い(リンク機構の固定部分)
- 3D CADの方を φ8.1±0.05mmに変更

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

### 2. 3D CADと2D図面の穴の違い(リンクの穴)
- 3D CADの方を φ24.1±0.05に変更
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

### 3. 更新した3D図面の提供　←今ここ(25/05/07)
- 製造中のミスを防ぐために，更新した3 図面の提供してほしいとのこと．
↓
- 以下の更新したファイルを提供
どちらを提供しましたか？
https://github.com/open-rdc/Bipedal_Robot_Hardware/blob/Hardware_sub/20250507.zip
or
https://github.com/open-rdc/Bipedal_Robot_Hardware/blob/Hardware_sub/20250507%20(2).zip

HarukiOgawa1, 2025-05-08:
25/05/07　←今ここ
### 内容
- ZIPファイルにはパーツが1つだけではないようです。ご確認の上、正しいパーツをお送りいただけますでしょうか？

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

@tomoki057
https://github.com/open-rdc/Bipedal_Robot_Hardware/issues/45#issuecomment-2862009220 の更新した部品の3D CADだけ送るようにしてください．
今回はgithubにzipファイルだと何をアップしたかわからないので，研究室の共有ドライブに発注するディレクトリを作って
@yasuohayashibara が発注，連絡しやすいようにしてください．

tomoki057, 2025-05-09:
ドライブに更新したiptファイルを送信しました。

HarukiOgawa1, 2025-05-10:
@tomoki057
ありがとうございます．

今回のメール内容だとBR2_parts_06.stpのデータを求められているため，
@yasuohayashibara
Slackと同じですが，BR2_parts_06.stpのCADデータを送付していただきたいです．

tomoki057, 2025-05-11:
更新したものをBR4_parts06(1)として送信しました.
確認よろしくお願いします.

yasuohayashibara, 2025-05-12:
Dear Quincy,

Thank you for your message.

I apologize for the confusion. It appears that I mistakenly included multiple files in the previous ZIP archive. I have now prepared a new file containing only the correct 3D model that reflects the specified hole diameter of φ24.1±0.05 mm.

Please find the corrected file attached for your review.

If you encounter any further issues or need additional information, please don’t hesitate to contact me.

Thank you again for your kind support.

Best regards,
Yasuo Hayashibara

[BR2_parts_06.zip](https://github.com/user-attachments/files/20153127/BR2_parts_06.zip)

yasuohayashibara, 2025-05-12:
Dear Yasuo,

Thank you for further update!

We can confirm that we have successfully received below file. Will forward to our engineers to review.

If there are any issues or further clarifications needed, we will reach out to you.

Thanks!

Best Regards

Quincy

HarukiOgawa1, 2025-05-12:
https://github.com/open-rdc/Bipedal_Robot_Hardware/issues/45#issuecomment-2870540215
BR2_parts_06.stpは↓のパーツなのであっていると思います．
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

HarukiOgawa1, 2025-05-20:
納品書の出し方
注文履歴の「Shopping documents」をダウンロードする．

以下の写真は公式チャットで出力された写真
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

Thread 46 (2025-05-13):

Power側回路の組み立て＆検査

Yusuke-Yamasaki-555, 2025-05-13:
タイトルママ。想定通りの動きになるのか、ロボットに詰める前に検査を行う。
同時に、回路ケース内での配置と配線も行う。

Yusuke-Yamasaki-555, 2025-05-20:
Power側回路の検査を実施

リレー接点側に5V、リレーコイル側に12Vを印加し、回路が想定通りかを検査した。

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

結果、非常停止ボタンのON、OFFで分岐端子台のVCC - GND間の電位差が5V - 0V付近に切り替わることを確認できた。結果、正常な動作ができていると判断した。

次、接点側に40Vにして同じ検査をした。
結果、問題なく行けた。

記録事項として、OFFの際に電位差は0V付近になるが、おおよそ1.2Vぐらいになっていたと記憶している。これはダイオードモジュールの仕様かも（未調査）。漏れ電圧ってやつ？
まあ、logicは置かないので大丈夫じゃないかな？

Yusuke-Yamasaki-555, 2025-06-10:
Power側は特に問題なさそうなので、Close。

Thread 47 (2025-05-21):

ハードウェア(胴体)の発注記録

akitonoguchi, 2025-05-21:
胴体を製作するにあたって購入する物品について確認する

akitonoguchi, 2025-05-21:
購入予定
https://docs.google.com/spreadsheets/d/1beK89e6c4xFrkDasppnH_tKjGbs9eiSKlh2Fypl1lrU/edit?usp=sharing

購入するにあたって考えた板の加工の割り振り
[製作概要1.pdf](https://github.com/user-attachments/files/20359530/1.pdf)

[製作概要2.pdf](https://github.com/user-attachments/files/20359531/2.pdf)

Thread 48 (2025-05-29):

豆腐の設計

HarukiOgawa1, 2025-05-29:

HarukiOgawa1, 2025-05-29:
コーナーガードは角だけでなくプラダン全体に貼る
ただし、カメラや緊急停止ボタン用、ロボットの支え紐、空気穴は空ける

yasuohayashibara, 2025-05-29:
どのような役割を持たせるかにもよりますが，転倒時に壊れないようにするのであれば強度を意識した設計を行う必要があります．
持つところがありません．安全な距離を保って持ち上げられるようにすることが必要だと思います．

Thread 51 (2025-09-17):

腰部の設計への指摘

yasuohayashibara, 2025-09-17:
腰部の設計をチェックしました．
致命的な問題は無いと思いますが，いくつか細かなところで指摘があります．
確認したら閉じてください．

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

１）切削したままだと手を切ると思いますので，後加工でヤスリをかけるか，クッションを取り付けてください．

２）こちらにはキャップを取り付けてください．（専用の部品があります）

３）上部との接合のためだと思いますが，狭いと入りませんので気をつけてください．
　　接合対象がプラスチックの場合はそれほど気にかけなくても大丈夫ですが．

４）ネジを付けたときに上部のパーツと干渉しないか確認してください．

Closed 2025-09-22.

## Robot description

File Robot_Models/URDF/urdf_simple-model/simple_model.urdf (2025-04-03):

<?xml version="1.0"?>

<robot name="rdc_biped_robot">


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

  <link name="base_link"/>
  <joint name="CPG" type="fixed">
    <parent link="base_link"/>
    <child link="body"/>
    <origin rpy="0 0 0" xyz="0 0 0.333"/>
  </joint>


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

  <link name="body">
    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
    <inertial>
      <origin xyz="0 0 0"/>
      <mass value="1.128279"/>
      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
    </inertial>
  </link>

  <joint name="luggage" type="fixed">
    <parent link="body"/>
    <child link="body_luggage"/>
    <origin rpy="0 0 0" xyz="-0.091 0 0"/>
  </joint>

  <link name="body_luggage">
    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
    <inertial>
      <origin xyz="0 0 0"/>
      <mass value="6.002284"/>
      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
    </inertial>
  </link>


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

  <joint name="r_waist_roll" type="revolute">
    <parent link="body"/>
    <child link="r_wr2wp"/>
    <origin rpy="0 0 0" xyz="-0.091 -0.075 0"/>
    <axis xyz="1 0 0"/>
    <limit effort="7.2" lower="-6.28" upper="6.28" velocity="11.519173063"/>
  </joint>

  <link name="r_wr2wp">
    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
    <inertial>
      <origin xyz="0 0 0"/>
      <mass value="1.463019"/>
      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
    </inertial>
 </link>

  <joint name="r_waist_pitch" type="revolute">
    <parent link="r_wr2wp"/>
    <child link="r_wp2kp"/>
    <origin rpy="0 0 0" xyz="0.091 -0.055 0.00"/>
    <axis xyz="0 1 0"/>
     <limit effort="7.2" lower="-6.28" upper="6.28" velocity="11.519173063"/>
  </joint>

  <link name="r_wp2kp">
    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
    <inertial>
      <origin xyz="0 0 0"/>
      <mass value="0.581098"/>
      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
    </inertial>
 </link>

  <joint name="r_knee_pitch" type="revolute">
    <parent link="r_wp2kp"/>
    <child link="r_kp2heel"/>
    <origin rpy="0 0 0" xyz="0 0 -0.16"/>
    <axis xyz="0 1 0"/>
     <limit effort="7.2" lower="-6.28" upper="6.28" velocity="11.519173063"/>
  </joint>
  
  <link name="r_kp2heel">
    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
    <inertial>
      <origin xyz="0 0 0"/>
      <mass value="0.199496"/>
      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
    </inertial>
 </link>

  <joint name="r_ankle" type="fixed">
    <parent link="r_kp2heel"/>
    <child link="r_heel2end"/>
    <origin rpy="0 0 0" xyz="0 0 -0.149335"/>
  </joint>

  <link name="r_heel2end">
     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
    <inertial>
      <origin xyz="0 0 0"/>
      <mass value="0.0"/>
      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
    </inertial>
  </link>


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

  <joint name="l_waist_roll" type="revolute">
    <parent link="body"/>
    <child link="l_wr2wp"/>
    <origin rpy="0 0 0" xyz="-0.091 0.075 0"/>
    <axis xyz="1 0 0"/>
    <limit effort="7.2" lower="-6.28" upper="6.28" velocity="11.519173063"/>
  </joint>

  <link name="l_wr2wp">
    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
    <inertial>
      <origin xyz="0 0 0"/>
      <mass value="1.463019"/>
      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
    </inertial>
 </link>

  <joint name="l_waist_pitch" type="revolute">
    <parent link="l_wr2wp"/>
    <child link="l_wp2kp"/>
    <origin rpy="0 0 0" xyz="0.091 0.055 0.00"/>
    <axis xyz="0 1 0"/>
     <limit effort="7.2" lower="-6.28" upper="6.28" velocity="11.519173063"/>
  </joint>

  <link name="l_wp2kp">
    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
    <inertial>
      <origin xyz="0 0 0"/>
      <mass value="0.581098"/>
      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
    </inertial>
 </link>

  <joint name="l_knee_pitch" type="revolute">
    <parent link="l_wp2kp"/>
    <child link="l_kp2heel"/>
    <origin rpy="0 0 0" xyz="0 0 -0.16"/>
    <axis xyz="0 1 0"/>
     <limit effort="7.2" lower="-6.28" upper="6.28" velocity="11.519173063"/>
  </joint>
  
  <link name="l_kp2heel">
    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
    <inertial>
      <origin xyz="0 0 0"/>
      <mass value="0.199496"/>
      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
    </inertial>
 </link>

  <joint name="l_ankle" type="fixed">
    <parent link="l_kp2heel"/>
    <child link="l_heel2end"/>
    <origin rpy="0 0 0" xyz="0 0 -0.149335"/>
  </joint>
  
  <link name="l_heel2end">
     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
    <inertial>
      <origin xyz="0 0 0"/>
      <mass value="0.0"/>
      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
    </inertial>
  </link>

</robot>

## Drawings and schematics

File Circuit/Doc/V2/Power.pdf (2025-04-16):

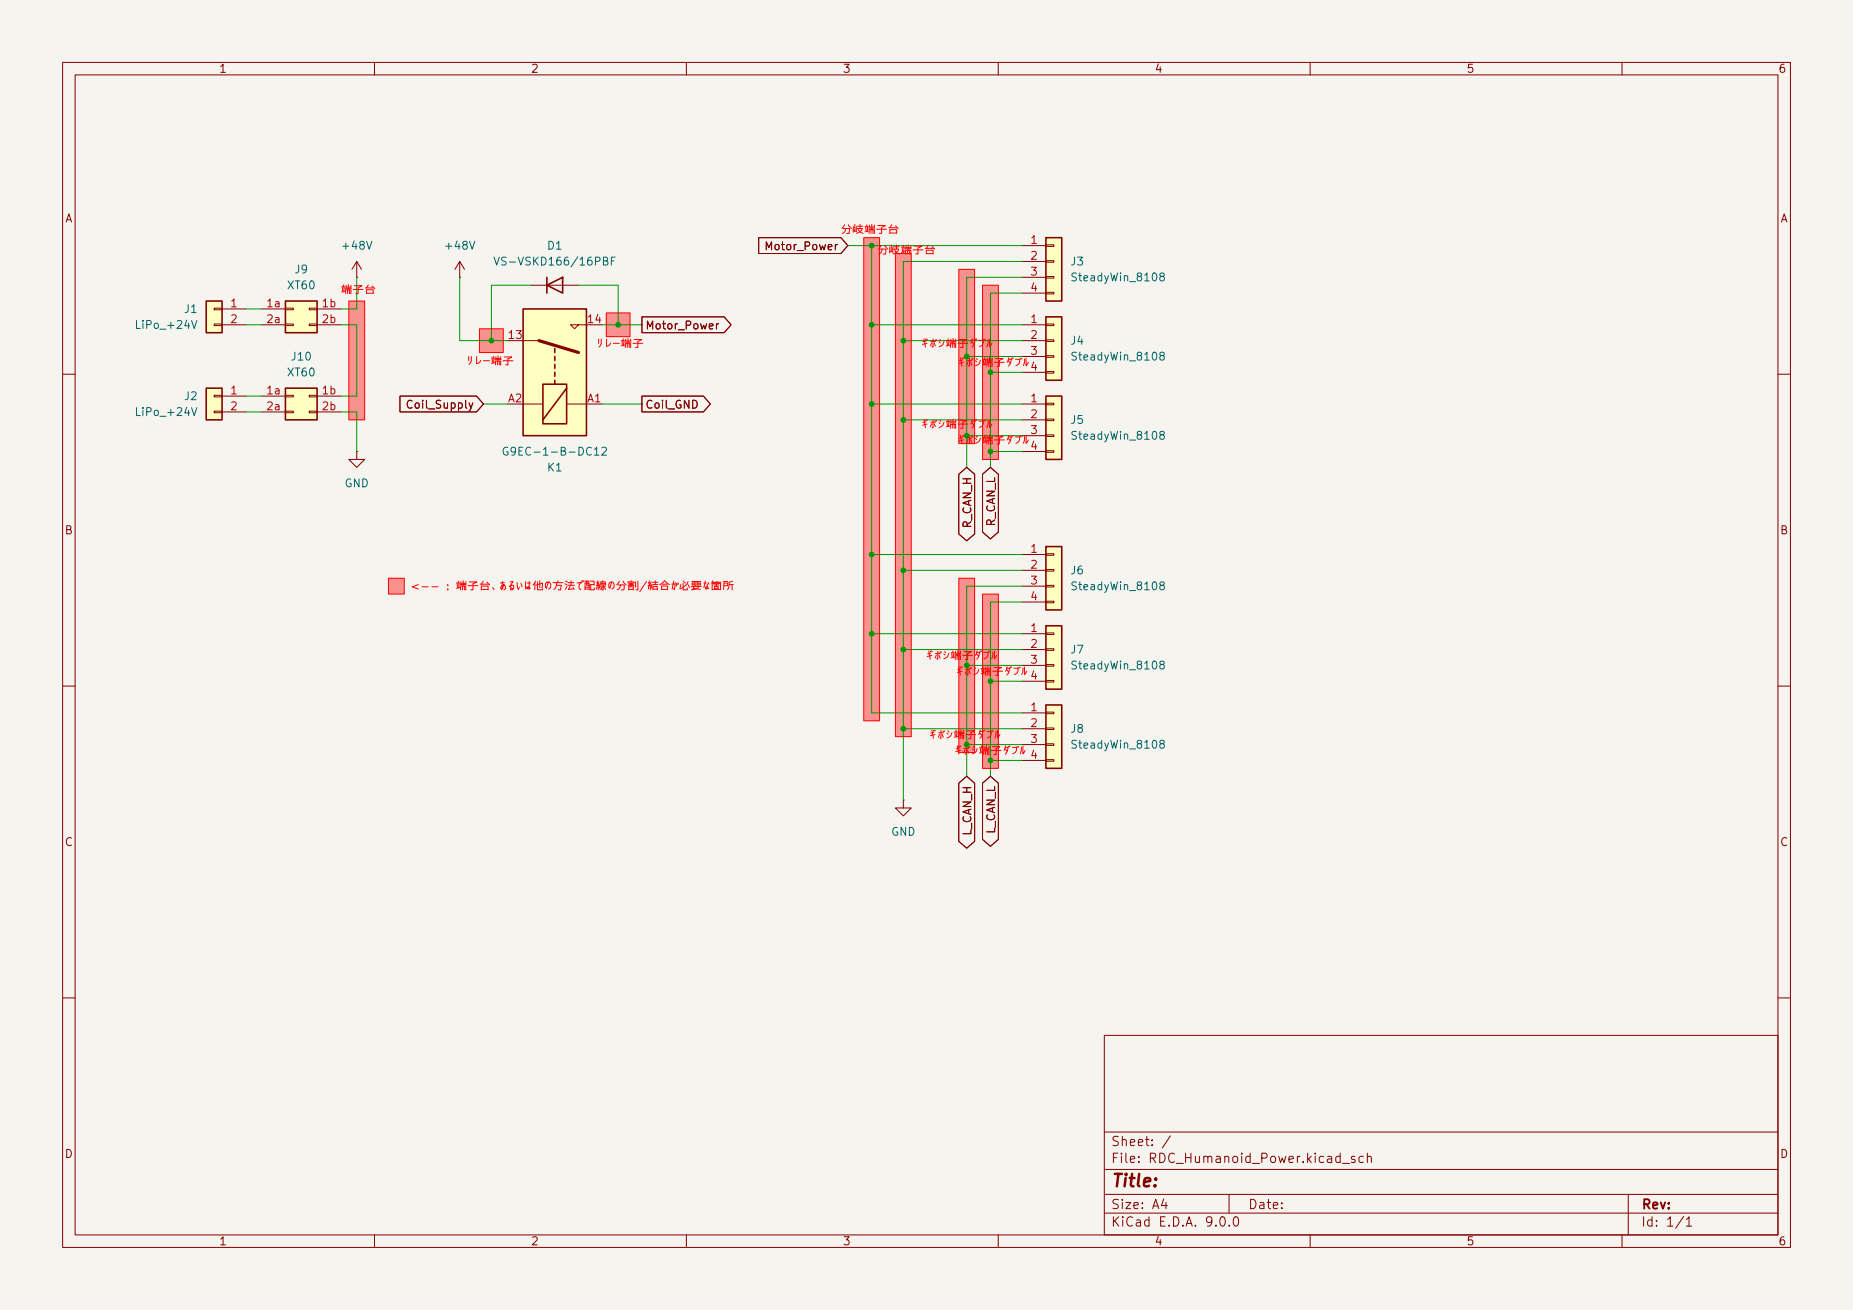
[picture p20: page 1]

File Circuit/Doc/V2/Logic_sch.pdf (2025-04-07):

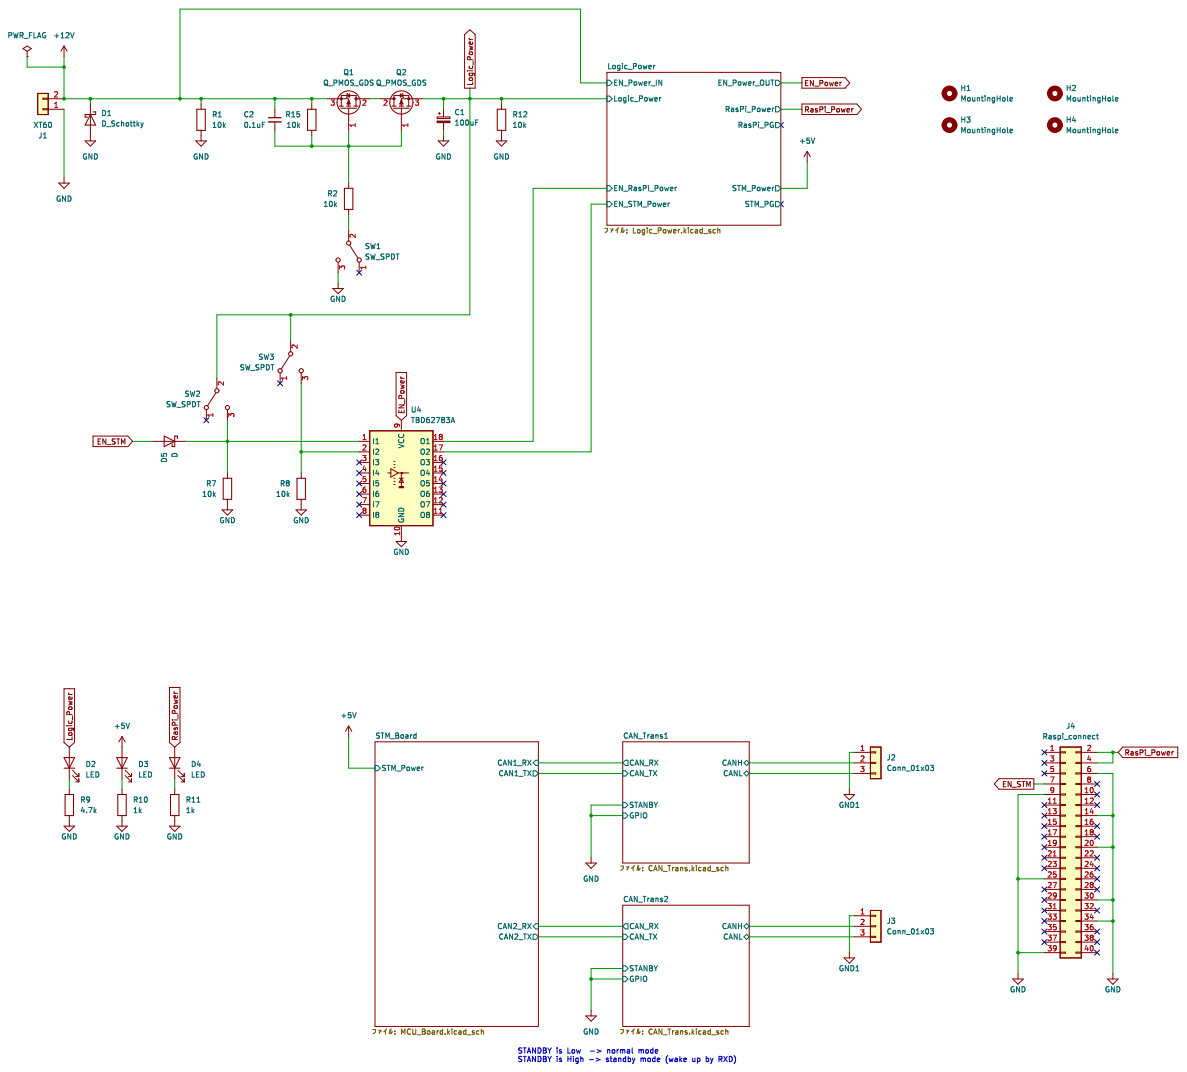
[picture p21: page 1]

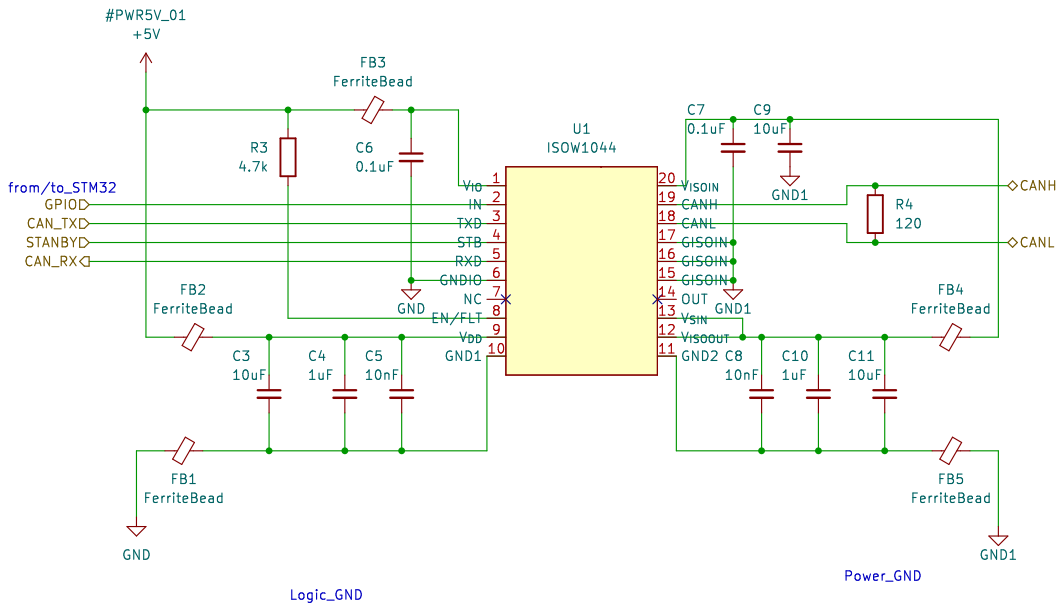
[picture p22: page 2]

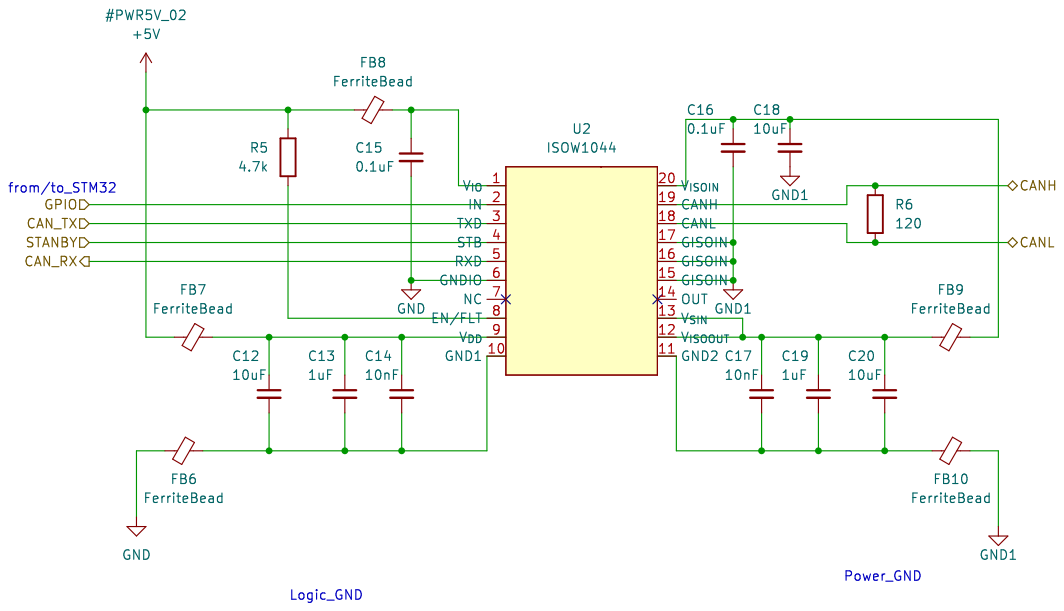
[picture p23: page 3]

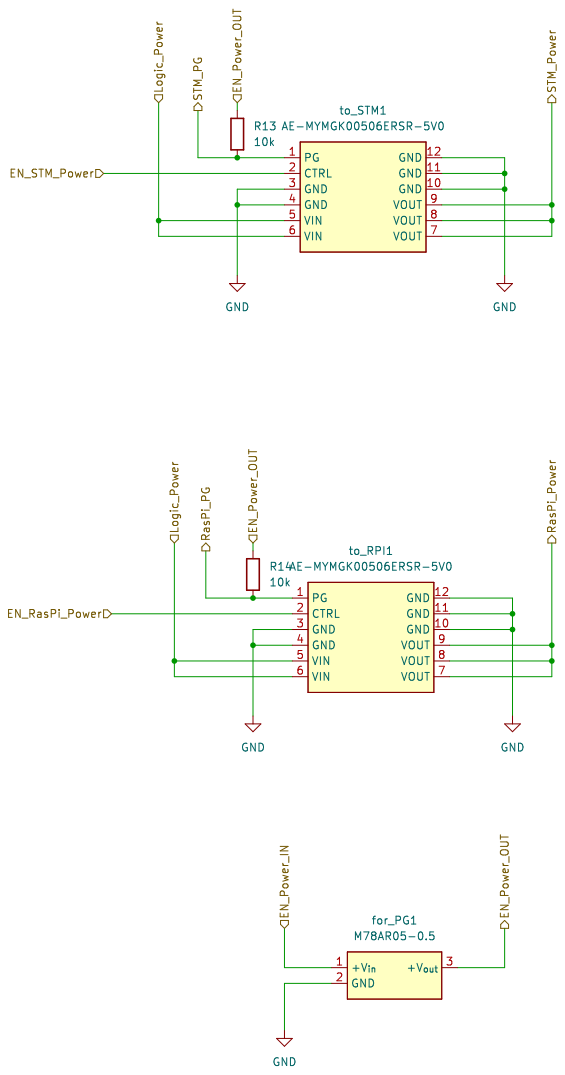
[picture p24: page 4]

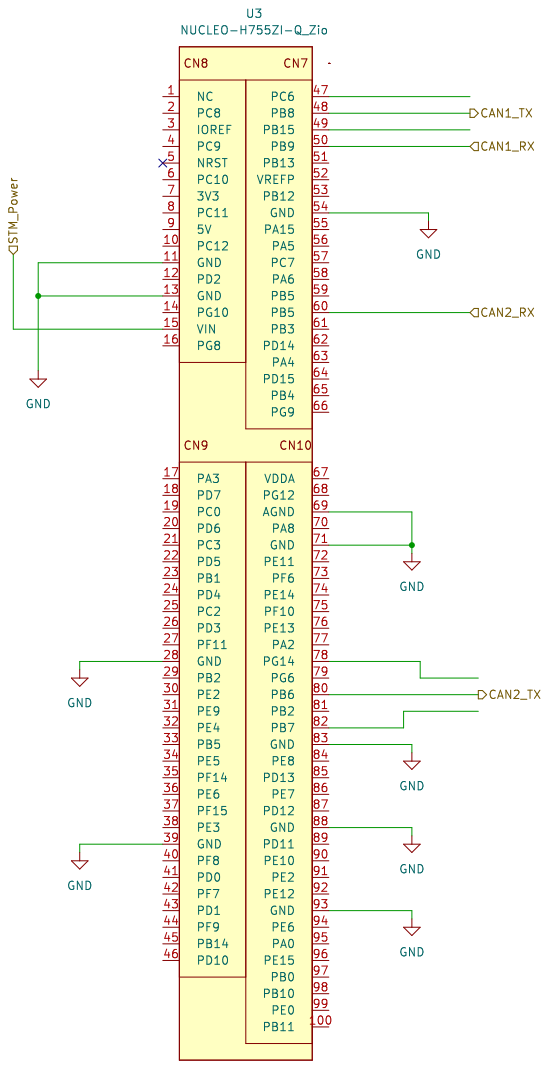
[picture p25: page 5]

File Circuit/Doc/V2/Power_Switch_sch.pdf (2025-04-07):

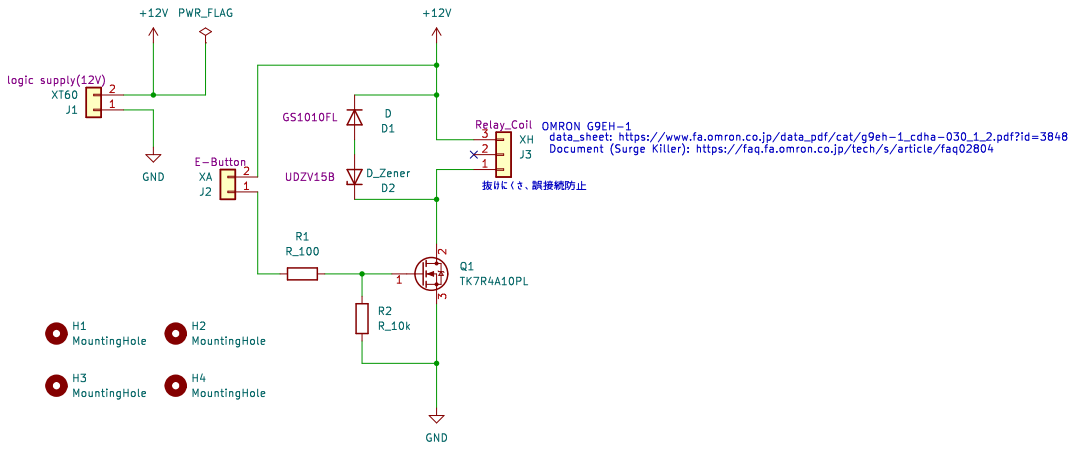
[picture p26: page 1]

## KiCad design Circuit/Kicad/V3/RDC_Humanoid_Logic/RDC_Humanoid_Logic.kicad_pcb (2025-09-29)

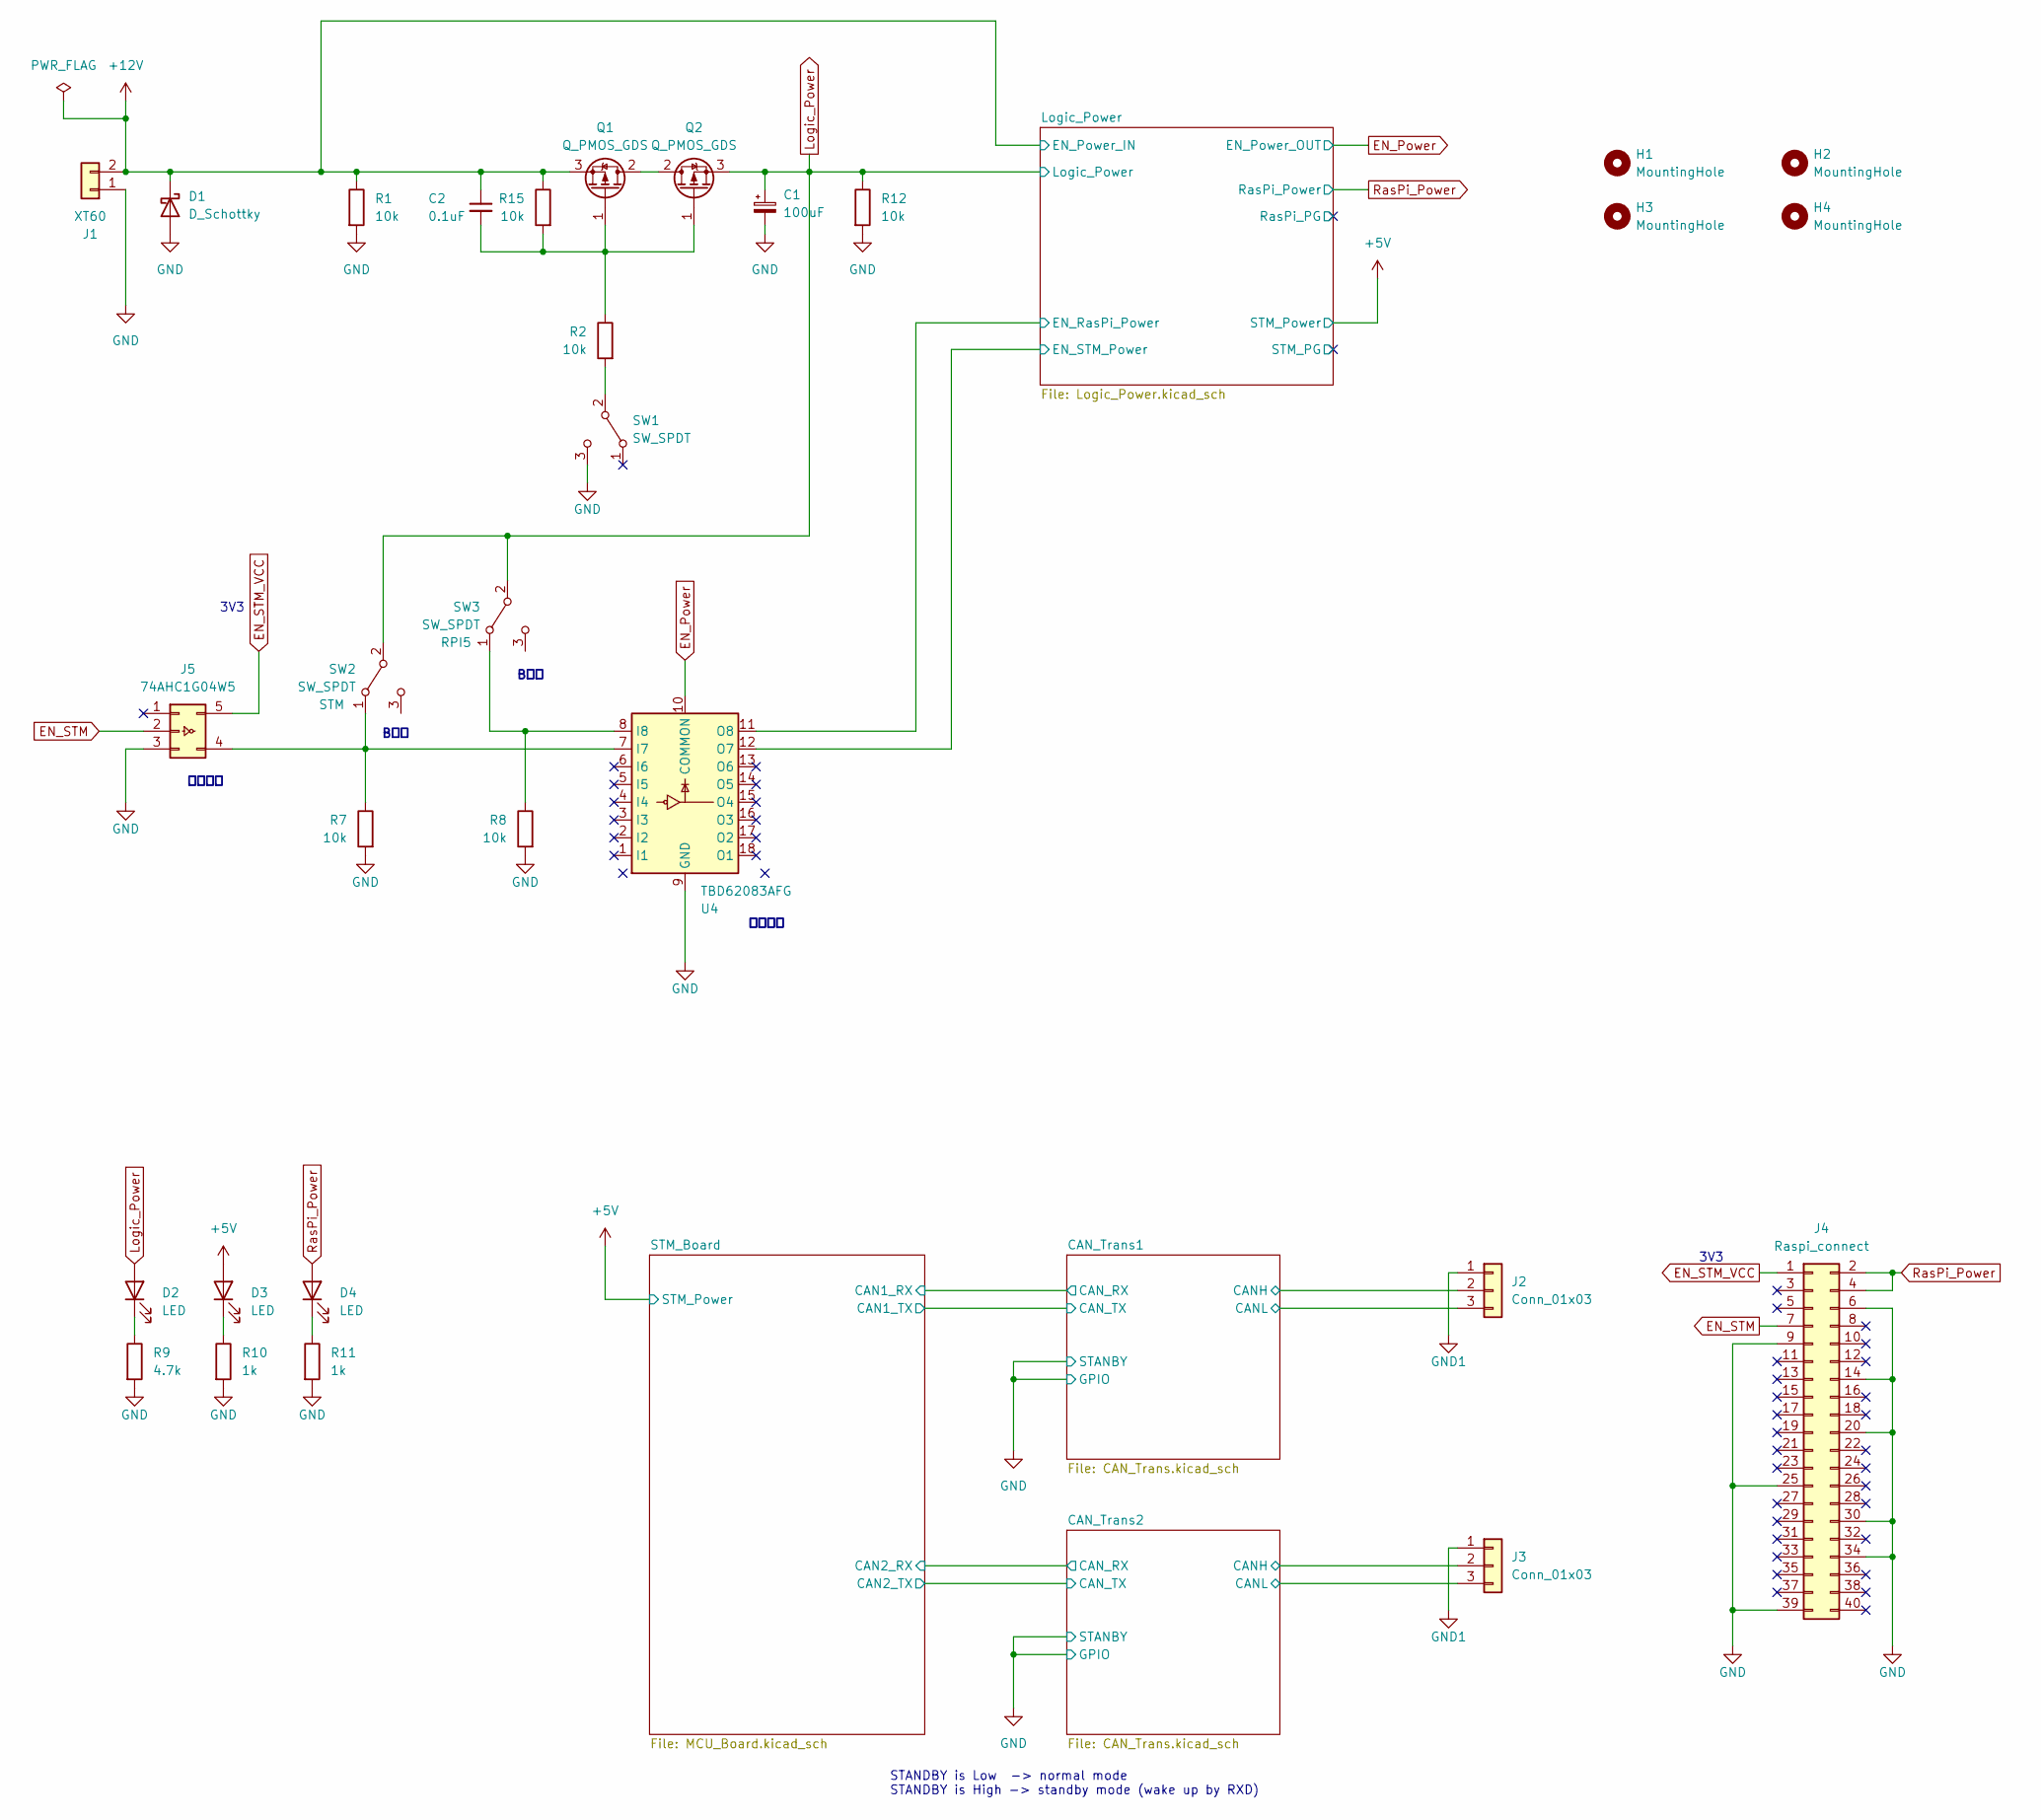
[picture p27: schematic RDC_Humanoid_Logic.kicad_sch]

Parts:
C1: 100uF; CP_Radial_D6.3mm_P2.50mm
C2: 0.1uF; C_0603_1608Metric
D1: D_Schottky; D_SOD-123
D2, D3, D4: LED; LED_0603_1608Metric
H1, H2, H3, H4: MountingHole; MountingHole_3.2mm_M3
J1: XT60; AMASS_XT60PW-M_1x02_P7.20mm_Horizontal
J2, J3: Conn_01x03; JST_XA_S03B-XASK-1_1x03_P2.50mm_Horizontal
J4: Raspi_connect; PinHeader_2x20_P2.54mm_Vertical
J5: 74AHC1G04W5; SOT-23-5
Q1, Q2: Q_PMOS_GDS; TO-252-2
R1, R2, R7, R8, R12, R15: 10k; R_0603_1608Metric
R9: 4.7k; R_0603_1608Metric
R10, R11: 1k; R_0603_1608Metric
SW1, SW2, SW3: SW_SPDT; Toggle_switch
U4: TBD62083AFG; SOP-18_7.495x11.515mm_P1.27mm

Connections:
+5V: D3.2 (A); also elsewhere on the board
+12V: C2.1, D1.1 (K), J1.2, Q1.3 (S), R1.1, R15.1; also elsewhere on the board
/CAN_Trans1/CANH: J2.2; also elsewhere on the board
/CAN_Trans1/CANL: J2.3; also elsewhere on the board
/CAN_Trans2/CANH: J3.2; also elsewhere on the board
/CAN_Trans2/CANL: J3.3; also elsewhere on the board
/Logic_Power/EN_RasPi_Power: U4.11 (O8); also elsewhere on the board
/Logic_Power/EN_STM_Power: U4.12 (O7); also elsewhere on the board
EN_Power: U4.10 (COMMON); also elsewhere on the board
EN_STM: J4.7, J5.2
EN_STM_VCC: J4.1, J5.5
GND: C1.2, D1.2 (A), J1.1, J4.6, J4.9, J4.14, J4.20, J4.25, J4.30, J4.34, J4.39, J5.3, R1.2, R7.2, R8.2, R9.2, R10.2, R11.2, R12.2, SW1.3 (C), U4.9 (GND); also elsewhere on the board
GND1: J2.1, J3.1; also elsewhere on the board
Logic_Power: C1.1, D2.2 (A), Q2.3 (S), R12.1, SW2.2 (B), SW3.2 (B); also elsewhere on the board
unnamed: D2.1 (K), R9.1
unnamed: D3.1 (K), R10.1
unnamed: D4.1 (K), R11.1
unnamed: J5.4, R7.1, SW2.1 (A), U4.7 (I7)
unnamed: Q1.2 (D), Q2.2 (D)
unnamed: C2.2, Q1.1 (G), Q2.1 (G), R2.1, R15.2
unnamed: R2.2, SW1.2 (B)
unnamed: R8.1, SW3.1 (A), U4.8 (I8)
RasPi_Power: D4.2 (A), J4.2, J4.4; also elsewhere on the board

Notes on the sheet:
B接点
修正済み
3V3
STANDBY is Low -> normal mode STANDBY is High -> standby mode (wake up by RXD)

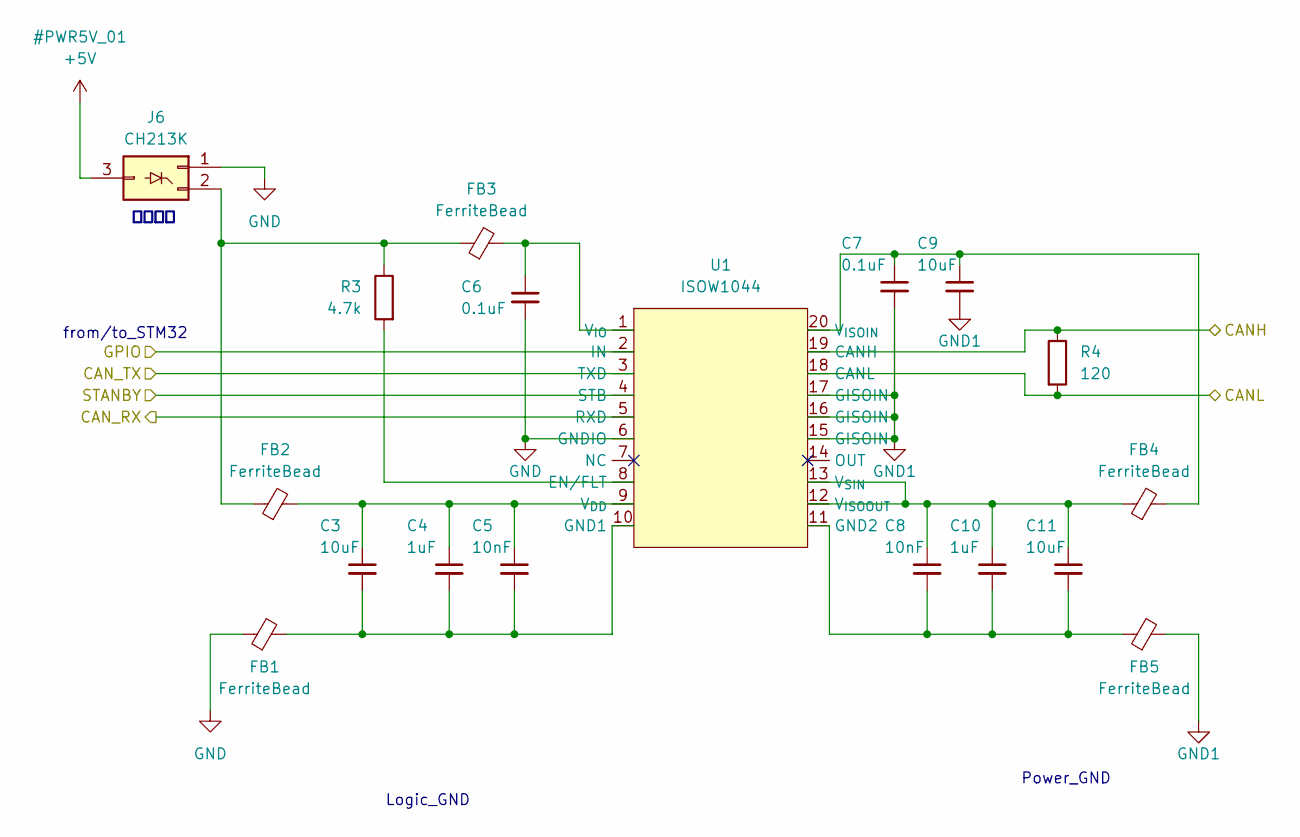
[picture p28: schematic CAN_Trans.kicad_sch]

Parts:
C3, C9, C11: 10uF; C_0603_1608Metric
C4, C10: 1uF; C_0603_1608Metric
C5, C8: 10nF; C_0603_1608Metric
C6, C7: 0.1uF; C_0603_1608Metric
FB1, FB2, FB3, FB4, FB5: FerriteBead; L_0805_2012Metric
J6: CH213K; SOT-23-3
R3: 4.7k; R_0603_1608Metric
R4: 120; R_0603_1608Metric
U1: ISOW1044; SOIC-20W_7.5x12.8mm_P1.27mm

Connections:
+5V: J6.3; also elsewhere on the board
/CAN_Trans1/CANH: R4.1, U1.19 (CANH); also elsewhere on the board
/CAN_Trans1/CANL: R4.2, U1.18 (CANL); also elsewhere on the board
/CAN_Trans1/CAN_RX: U1.5 (RXD); also elsewhere on the board
/CAN_Trans1/CAN_TX: U1.3 (TXD); also elsewhere on the board
GND: C6.2, FB1.1, J6.1, U1.2 (IN), U1.4 (STB), U1.6 (GNDIO); also elsewhere on the board
GND1: C7.2, C9.2, FB5.2, U1.15 (GISOIN), U1.16 (GISOIN), U1.17 (GISOIN); also elsewhere on the board
unnamed: FB2.1, FB3.1, J6.2, R3.1
unnamed: R3.2, U1.8 (EN/FLT)
unnamed: C3.2, C4.2, C5.2, FB1.2, U1.10 (GND1)
unnamed: C8.2, C10.2, C11.2, FB5.1, U1.11 (GND2)
unnamed: C3.1, C4.1, C5.1, FB2.2, U1.9 (V_{DD})
unnamed: C6.1, FB3.2, U1.1 (V_{IO})
unnamed: C7.1, C9.1, FB4.2, U1.20 (V_{ISOIN})
unnamed: C8.1, C10.1, C11.1, FB4.1, U1.12 (V_{ISOOUT}), U1.13 (V_{SIN})

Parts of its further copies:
C12, C18, C20: 10uF; C_0603_1608Metric
C13, C19: 1uF; C_0603_1608Metric
C14, C17: 10nF; C_0603_1608Metric
C15, C16: 0.1uF; C_0603_1608Metric
FB6, FB7, FB8, FB9, FB10: FerriteBead; L_0805_2012Metric
J7: CH213K; SOT-23-3
R5: 4.7k; R_0603_1608Metric
R6: 120; R_0603_1608Metric
U2: ISOW1044; SOIC-20W_7.5x12.8mm_P1.27mm

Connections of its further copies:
+5V: J7.3; also elsewhere on the board
/CAN_Trans2/CANH: R6.1, U2.19 (CANH); also elsewhere on the board
/CAN_Trans2/CANL: R6.2, U2.18 (CANL); also elsewhere on the board
/CAN_Trans2/CAN_RX: U2.5 (RXD); also elsewhere on the board
/CAN_Trans2/CAN_TX: U2.3 (TXD); also elsewhere on the board
GND: C15.2, FB6.1, J7.1, U2.2 (IN), U2.4 (STB), U2.6 (GNDIO); also elsewhere on the board
GND1: C16.2, C18.2, FB10.2, U2.15 (GISOIN), U2.16 (GISOIN), U2.17 (GISOIN); also elsewhere on the board
unnamed: FB7.1, FB8.1, J7.2, R5.1
unnamed: R5.2, U2.8 (EN/FLT)
unnamed: C12.2, C13.2, C14.2, FB6.2, U2.10 (GND1)
unnamed: C17.2, C19.2, C20.2, FB10.1, U2.11 (GND2)
unnamed: C12.1, C13.1, C14.1, FB7.2, U2.9 (V_{DD})
unnamed: C15.1, FB8.2, U2.1 (V_{IO})
unnamed: C16.1, C18.1, FB9.2, U2.20 (V_{ISOIN})
unnamed: C17.1, C19.1, C20.1, FB9.1, U2.12 (V_{ISOOUT}), U2.13 (V_{SIN})

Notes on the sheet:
修正済み
Logic_GND
from/to_STM32
Power_GND

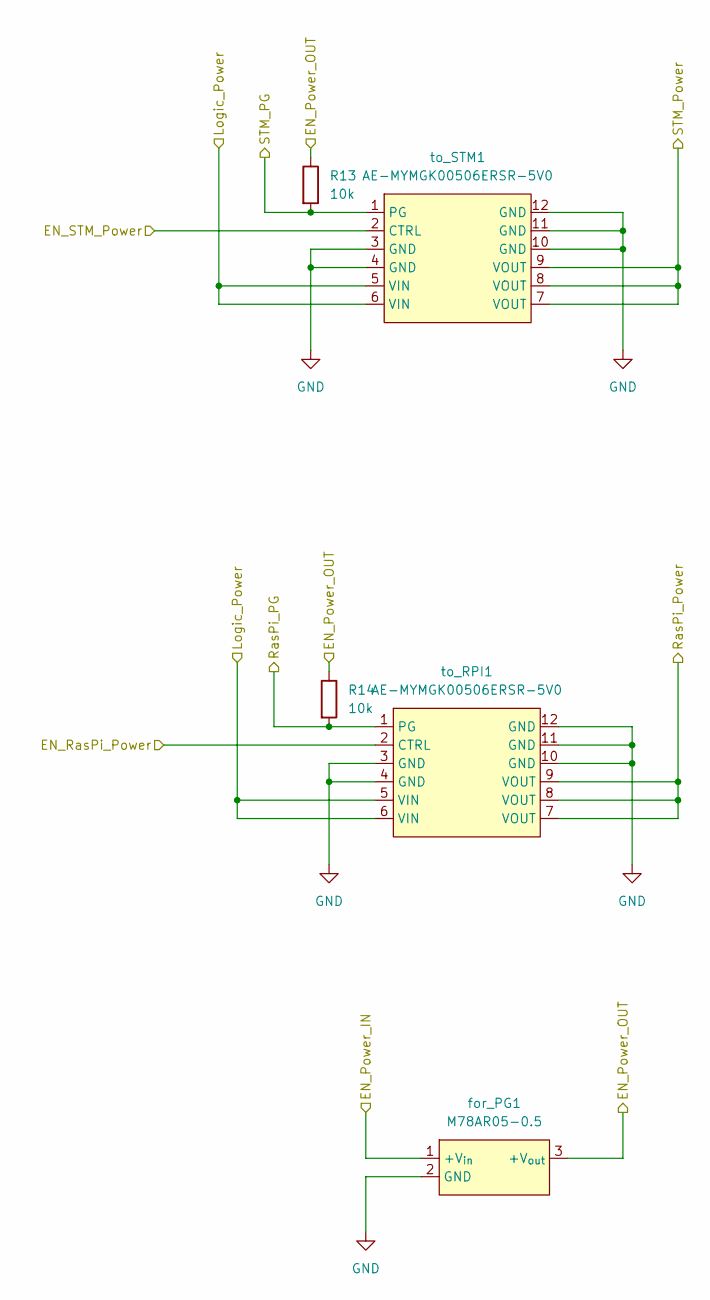
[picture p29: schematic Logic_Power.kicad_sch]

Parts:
R13, R14: 10k; R_0603_1608Metric
for_PG1: M78AR05-0.5; M78A
to_RPI1: AE-MYMGK00506ERSR-5V0
to_STM1: AE-MYMGK00506ERSR-5V0

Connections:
+5V: to_STM1.7 (VOUT), to_STM1.8 (VOUT), to_STM1.9 (VOUT); also elsewhere on the board
+12V: for_PG1.1 (+V_{in}); also elsewhere on the board
/Logic_Power/EN_RasPi_Power: to_RPI1.2 (CTRL); also elsewhere on the board
/Logic_Power/EN_STM_Power: to_STM1.2 (CTRL); also elsewhere on the board
/Logic_Power/RasPi_PG: R14.2, to_RPI1.1 (PG)
/Logic_Power/STM_PG: R13.2, to_STM1.1 (PG)
EN_Power: R13.1, R14.1, for_PG1.3 (+V_{out}); also elsewhere on the board
GND: for_PG1.2 (GND), to_RPI1.3 (GND), to_RPI1.4 (GND), to_RPI1.10 (GND), to_RPI1.11 (GND), to_RPI1.12 (GND), to_STM1.3 (GND), to_STM1.4 (GND), to_STM1.10 (GND), to_STM1.11 (GND), to_STM1.12 (GND); also elsewhere on the board
Logic_Power: to_RPI1.5 (VIN), to_RPI1.6 (VIN), to_STM1.5 (VIN), to_STM1.6 (VIN); also elsewhere on the board
RasPi_Power: to_RPI1.7 (VOUT), to_RPI1.8 (VOUT), to_RPI1.9 (VOUT); also elsewhere on the board

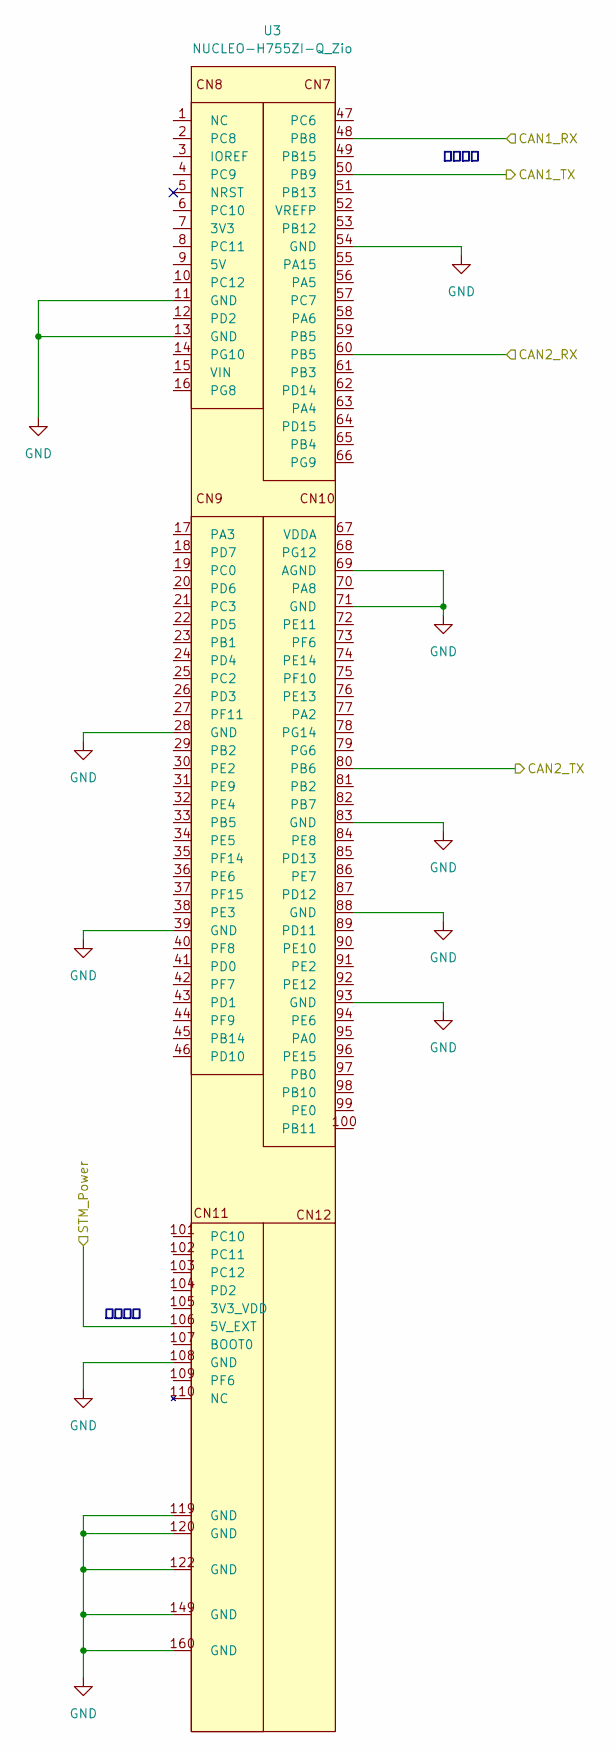
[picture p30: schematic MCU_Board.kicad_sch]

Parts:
U3: NUCLEO-H755ZI-Q_Zio; NUCLEO-STM32H755ZI-Q

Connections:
+5V: U3.106 (5V_EXT); also elsewhere on the board
/CAN_Trans1/CAN_RX: U3.48 (PB8); also elsewhere on the board
/CAN_Trans1/CAN_TX: U3.50 (PB9); also elsewhere on the board
/CAN_Trans2/CAN_RX: U3.60 (PB5); also elsewhere on the board
/CAN_Trans2/CAN_TX: U3.80 (PB6); also elsewhere on the board
GND: U3.11 (GND), U3.13 (GND), U3.28 (GND), U3.39 (GND), U3.54 (GND), U3.69 (AGND), U3.71 (GND), U3.83 (GND), U3.88 (GND), U3.93 (GND), U3.108 (GND), U3.119 (GND), U3.120 (GND), U3.122 (GND), U3.149 (GND), U3.160 (GND); also elsewhere on the board

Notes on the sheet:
修正済み

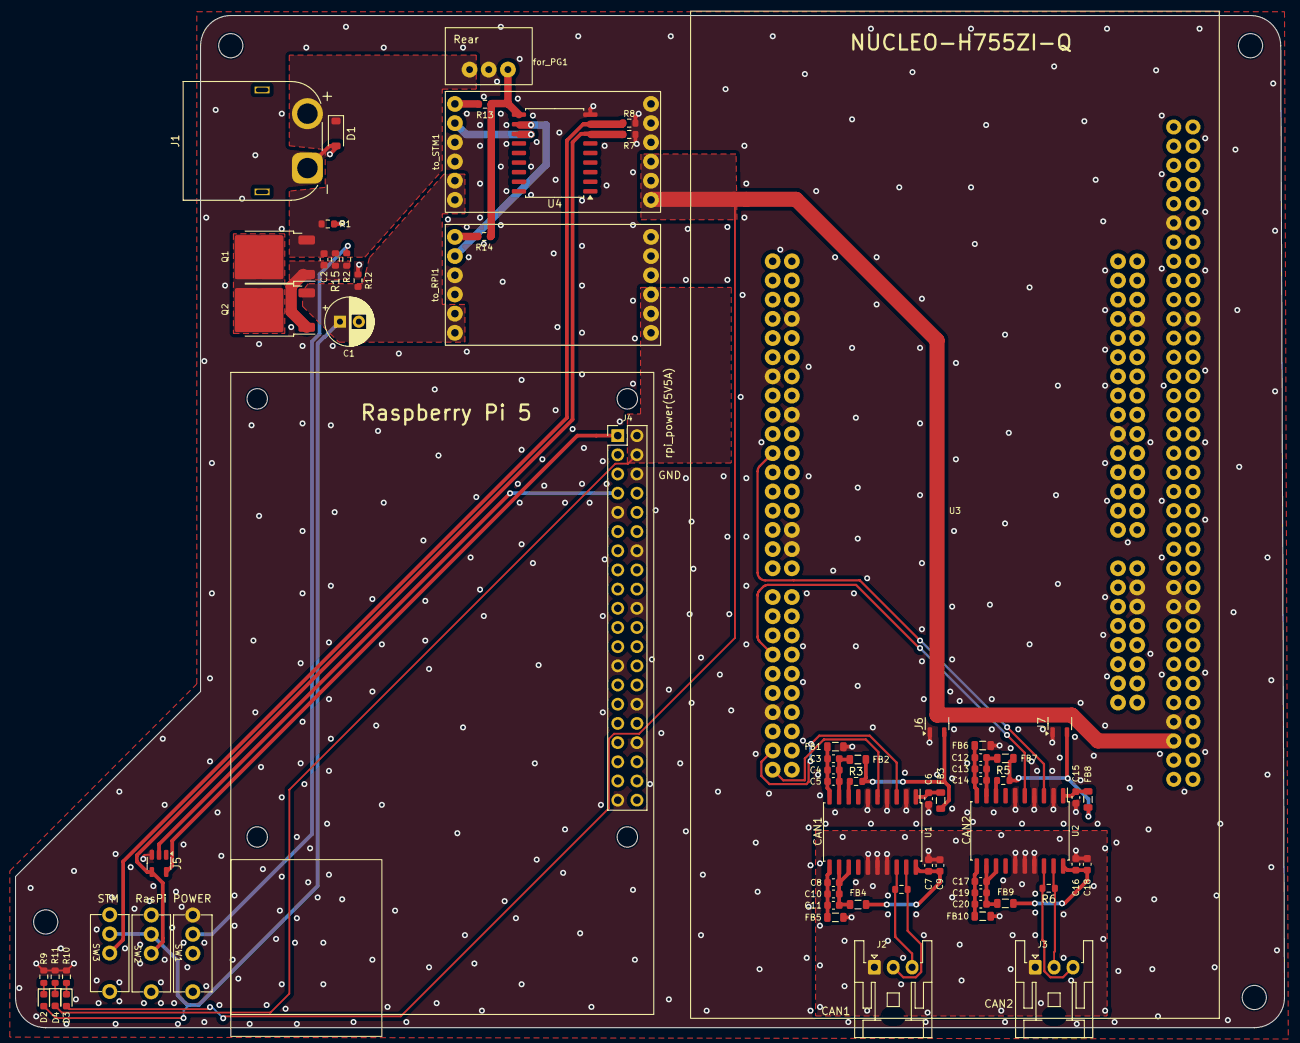
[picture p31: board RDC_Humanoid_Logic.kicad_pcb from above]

Board: 2 copper layers, 168.0 x 134.0 mm, 72 parts (0 on the bottom side), 45 nets.

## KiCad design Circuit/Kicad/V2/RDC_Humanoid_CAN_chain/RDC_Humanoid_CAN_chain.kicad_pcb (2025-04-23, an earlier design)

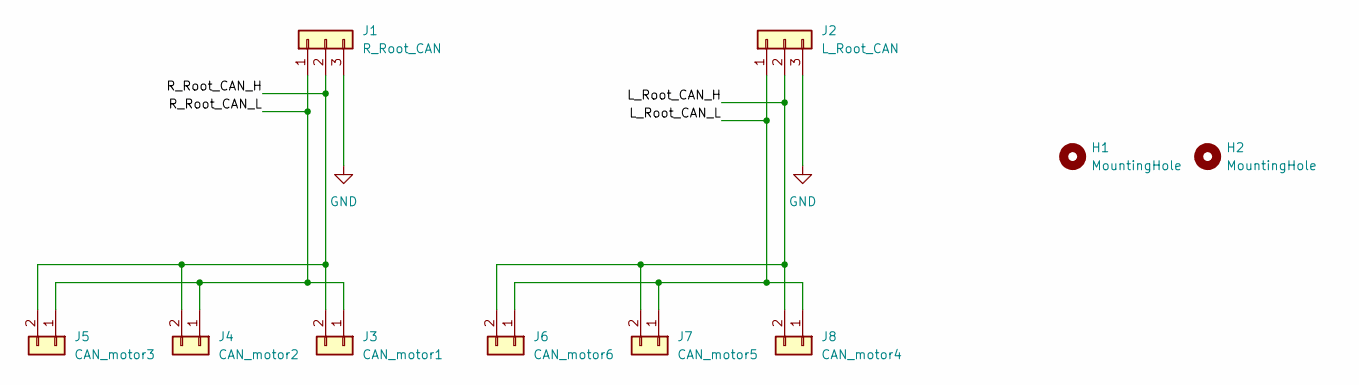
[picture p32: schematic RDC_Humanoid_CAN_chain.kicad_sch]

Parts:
H1, H2: MountingHole; MountingHole_3.2mm_M3
J1: R_Root_CAN; JST_XA_S03B-XASK-1_1x03_P2.50mm_Horizontal
J2: L_Root_CAN; JST_XA_S03B-XASK-1_1x03_P2.50mm_Horizontal
J3: CAN_motor1; JST_XA_S02B-XASK-1_1x02_P2.50mm_Horizontal
J4: CAN_motor2; JST_XA_S02B-XASK-1_1x02_P2.50mm_Horizontal
J5: CAN_motor3; JST_XA_S02B-XASK-1_1x02_P2.50mm_Horizontal
J6: CAN_motor6; JST_XA_S02B-XASK-1_1x02_P2.50mm_Horizontal
J7: CAN_motor5; JST_XA_S02B-XASK-1_1x02_P2.50mm_Horizontal
J8: CAN_motor4; JST_XA_S02B-XASK-1_1x02_P2.50mm_Horizontal

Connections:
/L_Root_CAN_H: J2.2, J6.2, J7.2, J8.2
/L_Root_CAN_L: J2.1, J6.1, J7.1, J8.1
/R_Root_CAN_H: J1.2, J3.2, J4.2, J5.2
/R_Root_CAN_L: J1.1, J3.1, J4.1, J5.1
GND: J1.3, J2.3

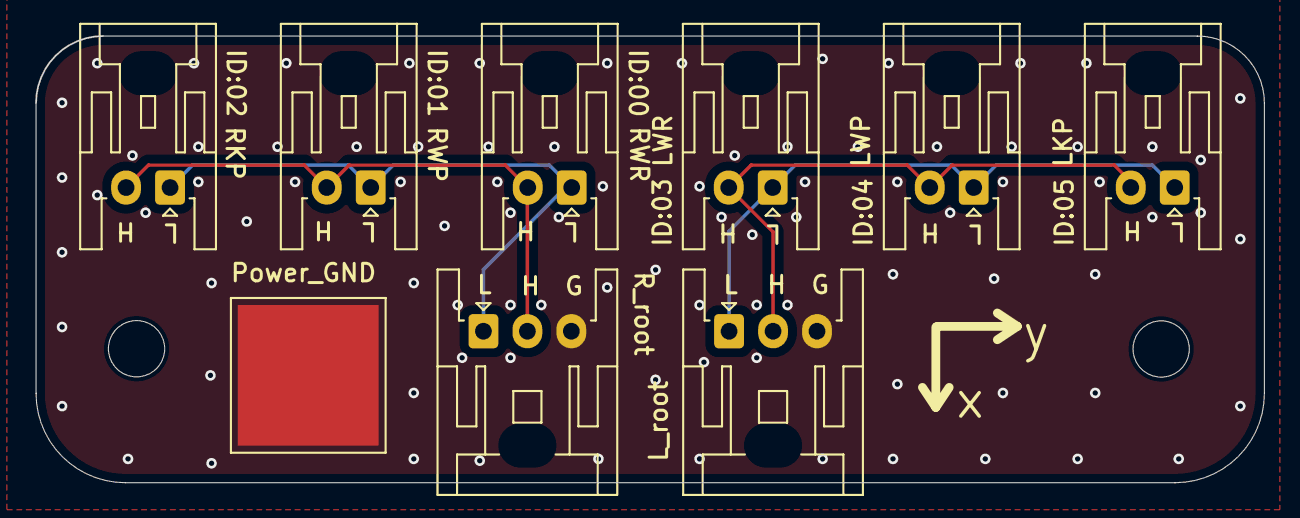
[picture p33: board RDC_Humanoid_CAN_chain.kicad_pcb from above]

Board: 2 copper layers, 69.9 x 25.4 mm, 10 parts (0 on the bottom side), 5 nets.

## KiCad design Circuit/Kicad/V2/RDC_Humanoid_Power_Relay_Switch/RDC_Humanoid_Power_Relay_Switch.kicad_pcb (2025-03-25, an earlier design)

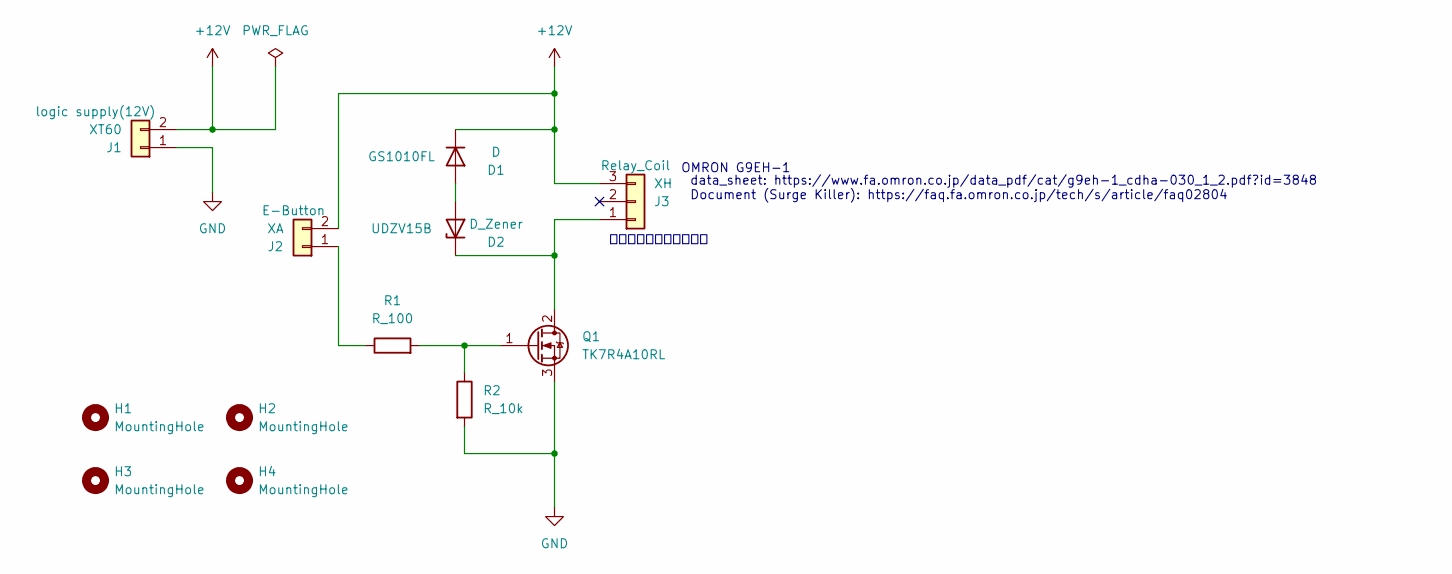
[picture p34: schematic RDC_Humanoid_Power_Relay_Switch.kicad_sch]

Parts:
D1: D; D_SOD-123
D2: D_Zener; D_SOD-323
H1, H2, H3, H4: MountingHole; MountingHole_3.2mm_M3
J1: XT60; AMASS_XT60PW-M_1x02_P7.20mm_Horizontal
J2: XA; JST_XA_S02B-XASK-1_1x02_P2.50mm_Horizontal
J3: XH; JST_XH_B3B-XH-A_1x03_P2.50mm_Vertical
Q1: TK7R4A10RL; TO-220-3_Vertical
R1: R_100; R_0603_1608Metric
R2: R_10k; R_0603_1608Metric

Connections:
+12V: D1.1 (K), J1.2, J2.2, J3.3
GND: J1.1, Q1.3 (S), R2.2
unnamed: D1.2 (A), D2.2 (A)
unnamed: D2.1 (K), J3.1, Q1.2 (D)
unnamed: J2.1, R1.1
unnamed: Q1.1 (G), R1.2, R2.1

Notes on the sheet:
抜けにくさ、誤接続防止
data_sheet: https://www.fa.omron.co.jp/data_pdf/cat/g9eh-1_cdha-030_1_2.pdf?id=3848 Document (Surge Killer): https://faq.fa.omron.co.jp/tech/s/article/faq02804
OMRON G9EH-1

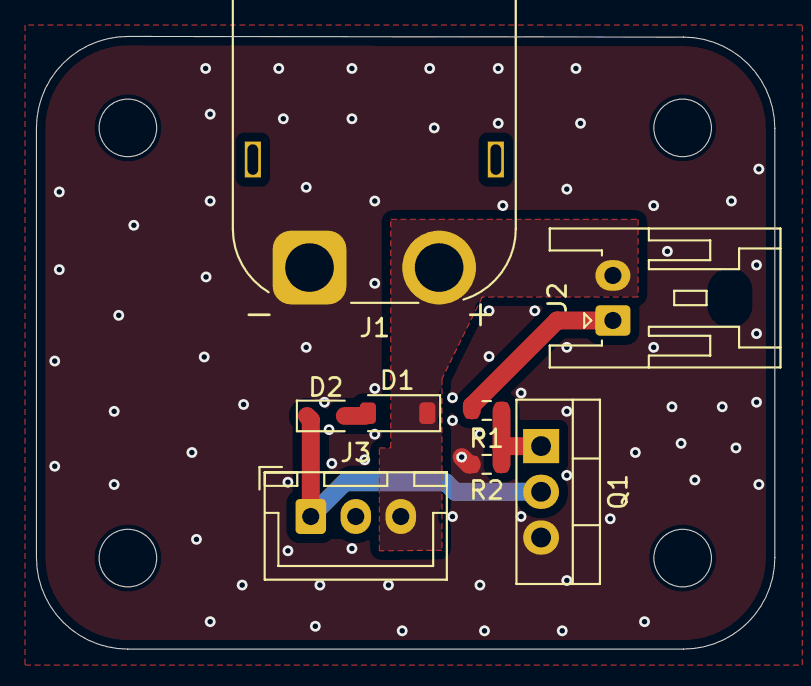
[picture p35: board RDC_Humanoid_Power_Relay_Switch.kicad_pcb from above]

Board: 2 copper layers, 41.0 x 34.0 mm, 12 parts (0 on the bottom side), 6 nets.

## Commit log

2025-01-17 ファイル場所の移動。URDF作成のためのDir整理
    [10mm_bearing.ipt, 10mm_bearing_MIR.ipt, 10mm_bearing_MIR1.ipt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]
2025-01-18 stlファイルの単位がダメだったので修正
    [b_right-wr2left-wr__legparts_09(six).stl, mb_right-wr2left-wr__legparts_09(six).stl, mr_j_kp__8108-8.stl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]
2025-01-18 原点を変えた。ただ座標系は変えられない。
    [b_right-wr2left-wr__legparts_09(six).stl, r_j_wp2kp__legparts_01.stl, r_j_wp2kp_stop_under__legparts_10.stl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]
2025-01-18 簡易モデル用のIPT＆STLを作成した。
    [body.ipt, body.stl, link_kp2heel.ipt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]
2025-01-18 未検証のURDFを作成
    [simple_model.urdf]
2025-01-18 inertiaの追加とpathの修正
    [simple_model.urdf]
2025-01-19 add wr2wp link
    [link_wr2wp_l.ipt, link_wr2wp_l.stl]
2025-01-19 簡易モデル（CAD、URDF）を作成した（質量と慣性は不正確）
    [simple_model.urdf]
2025-01-22 脛と足を別パーツ化
    [link_heel2end.ipt, link_heel2end.stl, link_kp2heel.0001.ipt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]
2025-01-23 add circuit v1 diagram (部品選定はまだ)
2025-01-27 全体の基本的な回路図の更新。Kicadでモータの電源周りのfootprintをテキトーに書いてみた。
    [test1.kicad_pcb, test1.kicad_sch]
2025-01-27 サージキラーが接点側についていたので、コイル側に修正
    [test1.kicad_sch]
2025-01-30 circuit version1.2
2025-01-31 Create Logic-Circuit Ver. 1.2.1 & Add part symbols for KiCad.
    [logic.kicad_pcb, logic.kicad_sch]
2025-02-01 高圧DCDCのラインを引いた
    [logic.kicad_sch]
2025-02-01 logicのsupply周りの回路のスケッチを書いた
    [logic.kicad_sch, logic_p2.kicad_sch, logic_p3.kicad_sch]
2025-02-05 version1.2.1のLogic周りの回路図を書いた
    [logic.kicad_sch, logic_p2.kicad_sch, logic_p3.kicad_sch]
2025-02-06 footprintを一部追加
    [logic.kicad_sch, logic_p2.kicad_sch, logic_p3.kicad_sch]
2025-02-06 FBとチップセラミックコンデンサを選定し、footprintを作成。
2025-02-06 チップ抵抗のfootprintを追加
    [logic.kicad_sch, logic_p2.kicad_sch]
2025-02-13 LogicのPCBを途中まで作った
    [logic.kicad_pcb, logic.kicad_sch, logic_p2.kicad_sch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]
2025-02-21 can_transceiver周りのPCBを作った（仮）
    [logic.kicad_pcb]
2025-02-24 can回路にLEDを追加。整理。
    [logic.kicad_pcb, logic.kicad_sch, logic_p2.kicad_sch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]
2025-02-27 スイッチの追加と整理。
    [logic.kicad_pcb, logic.kicad_sch, logic_p2.kicad_sch]
2025-03-01 Version1のLogic基板が、形はできた。検査や見積もりはまだ
    [logic.kicad_pcb, logic.kicad_sch, logic_p2.kicad_sch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]
2025-03-06 シルクを直した
    [logic.kicad_pcb]
2025-03-06 v1-3ぐらい
    [logic.kicad_pcb]
2025-03-07 power側の回路図を作成。ヒューズ無しバージョン
2025-03-08 Logic回路Ver2の作成開始。アドバイスを元に、参考回路をほぼ丸々コピーして作成する予定
    [logic_circuit.kicad_pcb, logic_circuit.kicad_sch]
2025-03-09 制御回路V2を追加
    [CAN_Trans.kicad_sch, Logic_Power.kicad_sch, MCU_Board.kicad_sch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]
2025-03-09 よくわからんV1の変化をコミット
2025-03-11 V2をUpdate。FrontをベタGND、CANトランシーバのSTANDBYとINをGNDに接続、ビアを複数配置、XT30->XT60に更新、D1を回路図通りショットキーバリアダイオードに変更した。
    [Logic_Power.kicad_sch, MCU_Board.kicad_sch, RDC_Humanoid_Logic.kicad_pcb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]
2025-03-11 リレーのスイッチング＆サージキラーの回路図を組んだ
    [RDC_Humanoid_Power_Relay_Switch.kicad_pcb, RDC_Humanoid_Power_Relay_Switch.kicad_sch]
2025-03-13 V2基板手直し
    [CAN_Trans.kicad_sch, RDC_Humanoid_Logic.kicad_pcb, RDC_Humanoid_Logic.kicad_sch]
2025-03-14 ビアを増やした。おおよそV2は良いだろう
    [RDC_Humanoid_Logic.kicad_pcb]
2025-03-16 部品表の作成、多少のFootPrint、PCBの変更
    [250317_logic_circuit_v2_parts_list.csv, CAN_Trans.kicad_sch, RDC_Humanoid_Logic.kicad_pcb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]
2025-03-20 gbrの生成
    [RDC_Humanoid_Logic-B_Cu.gbr, RDC_Humanoid_Logic-B_Mask.gbr, RDC_Humanoid_Logic-B_Paste.gbr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]
2025-03-20 リレーコイルのスイッチ基板の回路図を起こした
    [RDC_Humanoid_Power_Relay_Switch.kicad_pcb, RDC_Humanoid_Power_Relay_Switch.kicad_sch]
2025-03-22 Relay_Switchの回路図とPCBを組んでみた。
    [RDC_Humanoid_Power_Relay_Switch.kicad_pcb, RDC_Humanoid_Power_Relay_Switch.kicad_sch]
2025-03-25 アドバイスを元に修正。Relay Switch用の基板ができた。
    [RDC_Humanoid_Power_Relay_Switch-B_Cu.gbr, RDC_Humanoid_Power_Relay_Switch-B_Mask.gbr, RDC_Humanoid_Power_Relay_Switch-B_Paste.gbr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]
2025-03-27 回路図のコメントの修正
    [RDC_Humanoid_Power_Relay_Switch.kicad_sch]
2025-04-01 回路置き場のモデルを作成した。URDF未適用
    [body_luggage.ipt, body_luggage.stl]
2025-04-03 Update Simple-Model-Mesh
    [body.0001.ipt, body.ipt, body.stl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]
2025-04-03 simple_modelに胴体を搭載。寸法・質量・慣性をUpdate。それっぽい感じになったのでよし。
    [simple_model.urdf]
2025-04-07 回路図をPDFに出力
2025-04-07 Power回路図を引いた
    [RDC_Humanoid_Power.kicad_pcb, RDC_Humanoid_Power.kicad_sch]
2025-04-15 CANのデイジーチェーン用基板を作成
    [RDC_Humanoid_CAN_chain.kicad_pcb, RDC_Humanoid_CAN_chain.kicad_sch]
2025-04-15 CANのデイジーチェーン用基板をUpdate
    [RDC_Humanoid_CAN_chain.kicad_pcb]
2025-04-16 power側の回路をUpdate
    [RDC_Humanoid_Power.kicad_sch]
2025-04-23 CAN_Chainにビア配置、テキスト整理。Gerberファイル出力
    [RDC_Humanoid_CAN_chain-B_Cu.gbr, RDC_Humanoid_CAN_chain-B_Mask.gbr, RDC_Humanoid_CAN_chain-B_Paste.gbr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]
2025-04-29 Logic V3 開始
    [CAN_Trans.kicad_sch, Logic_Power.kicad_sch, MCU_Board.kicad_sch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]
2025-05-31 logic V3のトランジスタアレイ周りを修正
    [CAN_Trans.kicad_sch, MCU_Board.kicad_sch, RDC_Humanoid_Logic.kicad_pcb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]
2025-07-04 修正箇所を修正した
    [CAN_Trans.kicad_sch, RDC_Humanoid_Logic.kicad_pcb]
2025-07-19 Update V3 logic. 回路図の更新完了。PCB途中
    [MCU_Board.kicad_sch, RDC_Humanoid_Logic.kicad_pcb]
2025-07-22 配線途中
    [RDC_Humanoid_Logic.kicad_pcb]
2025-07-29 Logic V.3の完了
    [RDC_Humanoid_Logic.kicad_pcb]
2025-09-29 ガーバーファイル生成
    [RDC_Humanoid_Logic-B_Cu.gbr, RDC_Humanoid_Logic-B_Mask.gbr, RDC_Humanoid_Logic-B_Paste.gbr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]
2026-01-30 commitし忘れをadd
    [RDC_Humanoid_Logic.csv]
2026-02-20 Create Hardware
    設計データ保管
